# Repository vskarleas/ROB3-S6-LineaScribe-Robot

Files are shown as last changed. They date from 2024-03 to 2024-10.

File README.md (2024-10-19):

# Projet ROB3: Rami, Yannis, Vasilis

## Description

On the S6 at polytech Sorbone (Robotics Engineering major) students are required to develop a robotic system from Scratch. Below is my realisation and development of such a robot that is called LineaScribe. For more information about the project objectives for the 2023-2024 academic year, visit the following link:  
[Robot objectives](https://wiki.fablab.sorbonne-universite.fr/BookStack/books/projets-due-2023-2024/page/le-sujet-du-projet). 

You can find the Fablab Wiki link of the project [here](https://wiki.fablab.sorbonne-universite.fr/BookStack/books/projets-due-2023-2024/page/projet-rob3-rami-yannis-vasilis)

---

## **LineaScribe Robot**

### **Informations**

#### Membres

| Nom Prénom | Email |
| --- | --- |
| TOBBAL Yannis | [tobbalya@gmail.com](mailto:tobbalya@gmail.com) |
| ARIDI Rami | [rami.aridi@etu.sorbonne-universite.fr](mailto:rami.aridi@etu.sorbonne-universite.fr) |
| SKARLEAS Vasileios Filippos | [vasileios.skarleas@etu.sorbonne-universite.fr]() |

#### Cursus

Polytech 3eme année | Spécialité: Robotique

#### Délais

Début: 14/02/24 | Fin: 23/05/24

### **But, objectifs et contexte**

#### But

Le but est de créer un robot capable de dessiner différentes formes sur une feuille de papier. Il doit pouvoir réaliser des formes préprogrammée ainsi qu'être contrôlé manuellement.

Le robot est fixé sur un support carré horizontal comportant une zone de dessin de 10\*10 cm. Il y a 2 exercice qu'il doit réussir. En outre, le robot faut être capable de répondre au cahier des charges disponible `<span style="text-decoration: underline;">`[ici](https://wiki.fablab.sorbonne-universite.fr/BookStack/books/projets-due-2023-2024/page/le-sujet-du-projet).

**`<span style="text-decoration: underline;">`Exercice 1
***Dessiner des formes prédéfinies*

Le robot doit être capable de réaliser en 10 +- 0.2 secondes:

-Une ligne droite de 5cm
-Une ligne droite de 5cm en pointillés
-Un cercle de 2.5cm de rayon
-Un cercle de 2.5cm de rayon en pointillés

`<span style="text-decoration: underline;">`**Exercice 2** *Permettre à un utilisateur de dessiner*`<span style="text-decoration: underline;">`

L'utilisateur doit être capable d'utiliser le robot pour dessiner la forme qu'il veut sur la zone de dessin. Le robot est contrôlé par un joystick qui doit donc être doté des fonctions utilisés dans l'exercice 1 (Déplacement, relever le stylo etc...)

#### Besoins

Il faut donc créer un robot qui:

- Maintienne un effecteur (le stylo) afin de dessiner
- Se déplace:
  - Dans un plan horizontal: Créer les formes
  - Verticalement: Dessiner ou non, pour les pointillés
- Enregistre des formes prédéfinies
- Soit capable d'être contrôlé précisément par le joystick

#### Matériel

Les moyens qu'on a à notre disposition sont les suivantes:

- Un crayon
- Interface de commande :
  - Une carte arduino UNO avec câble USB-B;
  - Un joystick:
  - Une platine de protoypage;
  - Alimentation régulée 5V ;
  - Câbles, LEDs, boutons poussoirs, résistances.
- Motorisation :
  - Deux servomoteurs HS422 180°;
  - Un servomoteur Emax ES08A 180°.
- Mécanique :
  - Matière PLA pour impression 3D;
  - Feuilles MDF : 3mm et 6mm d'épaisseur;
  - Vis et écrous : M2, M2.5, M3, M4.
  - Roulements et axes de diamètre 4mm.
- Informatique
  - Ressources CAO.zip contient les fichiers Solidworks pour les deux modèles de servomoteurs
  - datasheets.zip contient les documentations de quelques-uns des composants fourni

#### Machines utilisées

Utilisation de l'impression 3D pour des pièces sophistiquée et éventuellement de la technologie de découpe laser pour les autres pièces.

##### Matière consommée:

MDF: 64 cm`<sup>`3 `</sup>`(Bras) + 302 cm`<sup>`3 `</sup>`(Tour): 366 cm`<sup>`3`</sup>` total
PLA: 7.3 cm`<sup>`3 `</sup>`(Effecteur) + 9 cm`<sup>`3 `</sup>`(Actionneur) : 16.3 cm`<sup>`3 `</sup>`total

### **Diagramme de GANTT**

Il y a un lien interactif qui est mis à jour à chaque modification via [https://airtable.com/appVydj1BDLSFj432/shrm5Cjk0diMBPmgL](https://airtable.com/appVydj1BDLSFj432/shrm5Cjk0diMBPmgL)

(https://wiki.fablab.sorbonne-universite.fr/BookStack/uploads/images/gallery/2024-02/project-fablab-rob3-tasks-1.png)(https://wiki.fablab.sorbonne-universite.fr/BookStack/uploads/images/gallery/2024-02/project-fablab-rob3-tasks-2.png)

<p class="callout info">**Nota bene**  
Ce diagramme de GANTT est donnée à titre indicatif</p>

[Project FabLab ROB3 Tasks (GANTT).pdf](https://wiki.fablab.sorbonne-universite.fr/BookStack/attachments/549)

### **Étape 1: Brainstorming, idées de réalisation et analyse des risques**

Durant notre brainstorming: nous eûmes 5 idées que nous avons ultimement rejetées:

[`<span style="color: rgb(35, 111, 161);">`*Figure 1: Photo de notre tableau - juste pour démonstration. Explications sont disponibles ci-dessous*](https://wiki.fablab.sorbonne-universite.fr/BookStack/uploads/images/gallery/2024-02/img-6529.png)

`<span style="color: rgb(34, 34, 34); font-family: var(--font-heading, var(--font-body)); font-size: 1.666em; font-weight: 400;">`Idée 1 - Robot de roues

`<span style="text-decoration: underline;"><span style="color: rgb(0, 0, 0);">`Principe:

Un robot sur deux roues motorisées. Il peut faire de rotations en faisant tourner ses roues dans des directions opposées

- Le stylo est attaché au centre de de la plateforme.
- Les roues seraient contrôlées grâce aux 2 servomoteurs HS422 d'une façon similaire au robot E-PUC. Les servomoteurs sont connectés à la plateforme et aux roues via des biellettes ou des engrenages.
- Un servomoteur ES08A est utilisé pour contrôler le mécanisme de levée et de descente du stylo. Ce servomoteur est plus petit que les HS422 et peut être monté sur la plateforme à proximité du stylo.

`<span style="text-decoration: underline;"><span style="color: rgb(0, 0, 0);">`Croquis:

[](https://wiki.fablab.sorbonne-universite.fr/BookStack/uploads/images/gallery/2024-03/screenshot-2024-03-02-at-2-31-25-pm.png)[`<span style="color: rgb(126, 140, 141);"><span style="color: rgb(35, 111, 161);">`*Figure 2: Croquis du robot de* roues (type voiture avec une bille pour la stabilisation)](https://wiki.fablab.sorbonne-universite.fr/BookStack/uploads/images/gallery/2024-03/screenshot-2024-03-02-at-2-31-25-pm.png)

`<span style="text-decoration: underline;"><span style="color: rgb(0, 0, 0);">`Avantages:

- `<span style="color: rgb(0, 0, 0);">`Le robot est facile à contrôler avec un joystick (important pour la réalisation de l’exercice 2)
- `<span style="color: rgb(0, 0, 0);">`Sa construction et modélisation est simple

`<span style="text-decoration: underline;"><span style="color: rgb(0, 0, 0);">`Inconvénients: 

- On ne peut pas réaliser de trajectoires complexes. Le robot ne peut pas suivre des trajectoires complexes sans l'aide de capteurs odométrique.
- L'utilisation des servomoteurs empêcherait de faire rouler le robot indéfiniment. Cela ne serait pas un problème avec l'exercice 1. L'exercice 2 pourrait se révéler impossible à faire (Prenons par exemple un cas hyperbolique et fantaisiste: La forme à dessiner au joystick est une réplique de la Joconde. Le robot ne pourrait jamais faire ceci). Pour dépasser cet obstacle, il faudrait utiliser de roues avec une diamètre assez grande entraînant des complications aux glissements sur la surface.

#### Idée 2 - Robot XY (cartésien)

`<span style="text-decoration: underline;"><span style="color: rgb(0, 0, 0);">`Principe:

Un système similaire au fonctionnement d'une imprimante 3D:

- A l'aide d'un système de bielle manivelle, les deux servomoteurs HS422 commandent des liaisons glissières sur les axes x et y.
- La bielle tenant le stylo est elle même tenue par une bielle. Cette dernière se positionne sur la coordonnée de son axe, tandis que la bielle de l'effecteur choisit alors la deuxième coordonnée du point.
- Le servomoteur ES08A commande la levée et descente du stylo

`<span style="text-decoration: underline;"><span style="color: rgb(0, 0, 0);">`Croquis:

[image (1).png*Figure 3: Le croquis d'un robot cartésien*](https://wiki.fablab.sorbonne-universite.fr/BookStack/uploads/images/gallery/2024-03/image-1.png)

`<span style="text-decoration: underline;"><span style="color: rgb(0, 0, 0);">`Avantages:

- Cette solution ne présente pas de singularités dans sa configuration. De plus, les calculs sont simplifiés par le fait qu'on ne réfléchisse que sur le plan cartésien. Ce qui signifie qu'il peut atteindre toutes les positions du plan cartésien.
- Ce système permet un mouvement fluide et précis du stylo.
- Les calculs pour contrôler le robot sont simplifiés par le fait qu'on ne réfléchit que sur le plan cartésien sans faire ce changements de `<span style="color: rgb(0, 0, 0);">`bases.

`<span style="text-decoration: underline; color: rgb(0, 0, 0);">`Inconvénients:

- Le système de bielle-manivelle peut être plus lourd qu'un système à roues motorisées, ce qui peut affecter la performance du robot.
- Le système de bielle manivelle pourrait se révéler trop massif pour le robot.
- La solution consommerait beaucoup de matière

#### Idée 3 - Scissors mecanism

`<span style="text-decoration: underline; color: rgb(0, 0, 0);">`Principe:

Inspirés du "Scissors mechanism", on voudrait attacher deux servomoteurs à la base du mécanisme et un système de commande d'actionneur au point "STYLO". Cette solution présente des avantages telles que :

`<span style="text-decoration: underline; color: rgb(0, 0, 0);">`Croquis:

[image (3).png*Figure 4: Démonstration du mécanisme de ciseaux*](https://wiki.fablab.sorbonne-universite.fr/BookStack/uploads/images/gallery/2024-03/image-3.png)

`<span style="text-decoration: underline;"><span style="color: rgb(0, 0, 0); text-decoration: underline;">`Avantages:

- Le mécanisme "Scissors" permet d'avoir un espace d'écriture plus grand que les systèmes à roues motorisées ou à bielle-manivelle. Cela est dû à la tendance du mécanisme à s'étendre.
- De plus, ce mécanisme est particulièrement adapté à la création de cercles. La rotation des bras permet de dessiner des cercles de différentes tailles avec précision.
- En outre, le mécanisme "Scissors" permet de dessiner des lignes droites très précises dans le sens du mouvement du stylo.

`<span style="text-decoration: underline; color: rgb(0, 0, 0);">`Inconvénients:

- Malheureusement, cette solution présente également un inconvénient. Les mouvements étant plutôt révolutionnaires, créer des lignes droites verticales du stylo semble limité et dans certains cas extrêmes impossible.

#### Idée 4 - Point d'intersection

`<span style="text-decoration: underline; color: rgb(0, 0, 0);">`Principe:

Le robot sera doté d'un mécanisme de ciseaux alimenté par deux servomoteurs positionnés aux coins de la base d'écriture. Chacun entraînera la rotation d'une poutre, permettant des mouvements de glissement dans les deux directions du vecteur r de rotation,. Le point d'intersection des deux poutres (créant ainsi une liaison glissière complexe) serait équipé du stylo, assurant une couverture totale de la feuille grâce à cette configuration ingénieuse.

`<span style="text-decoration: underline; color: rgb(0, 0, 0);">`Croquis:

[*Figure 5: Une conception de l'idée de point d'intersection*](https://wiki.fablab.sorbonne-universite.fr/BookStack/uploads/images/gallery/2024-02/file-000.png)

`<span style="text-decoration: underline; color: rgb(0, 0, 0);">`Inconvénients:

- L'effort tangent au mouvement du stylo généré par une poutre sur l'autre serait extrêmement important, dépassant probablement les limites de faisabilité. La nécessité d'un glissement ultra-lisse, sans aucun frottement, et d'une précision extrême dans les mouvements représente un défi technique considérable.

#### Idée 5 - Robot type SCARA

`<span style="text-decoration: underline; color: rgb(0, 0, 0);">`Principe:

On a pensé de faire un robot qui a deux axes de rotation verticales et une axe de rotation horizontale. En fait, il y aura deux rotations autour de deux axes Z (Z1 et Z2) verticales et une troisième rotation autour de Z3 qui est perpendiculaire au axe (Z2).

`<span style="text-decoration: underline;">`Croquis:

[image (2).png*Figure 6: croquis du robot avec 2 dégrées de liberté*](https://wiki.fablab.sorbonne-universite.fr/BookStack/uploads/images/gallery/2024-03/image-2.png)

`<span style="text-decoration: underline;">`Avantages:

- C'est un modèle connu du groupe, la partie mathématique est donc plus simple à réaliser
- Il y a beaucoup de manières de retirer de la matière avec une modélisation intelligente.

`<span style="text-decoration: underline;">`Inconvénients:

- Poids excessive sur l'endroit du moteur 2, quelque chose qui pourrait impacter la précision de designs. Idéalement, on voudrait trouver une solution qui permettra de déplacer ce moteur sur le corps de la base principale du robot (où se trouve le moteur 1) en utilisant les outils qu'on a à notre disposition.

#### Idée 6 - Robot parallélépipède

`<span style="text-decoration: underline;">`Principe:

Inspiré par le mécanisme du robot type SCARA, on avait une réflexion: "Pourquoi on ne déplace pas le moteur de la 2éme rotation (moteur2), sur le même axe de rotation qui celui du moteur 1. Le résultat du mouvement sera la même tout en ayant déplacé la majorité du poids sur le corps principale du robot.

`<span style="text-decoration: underline;">`Croquis:

[Figure 7: Croquis du robot parallélépipède](https://wiki.fablab.sorbonne-universite.fr/BookStack/uploads/images/gallery/2024-03/Km2image.png)

`<span style="text-decoration: underline;">`Avantages:

- Moins de poids sur les articulations mobiles du robot =&gt; meilleur précision par rapport l'idée d'avant.

`<span style="text-decoration: underline;">`Inconvénients:

- Selon la manière d'expression du modèle géométrique direct, le calcul du modèle géométrique inverse pourrait être compliqué.
- La modélisation des quelques pièces unique pour la réalisation de ce type du robot pourrait augmenter le temps de fabrication et l'utilisation de matière.

#### Solution retenue

Ayant effectué une évaluation approfondie des différentes alternatives, notre équipe a choisi de privilégier le développement d'un robot type parallélépipède pour la prochaine étape du projet. Cette décision est basée sur plusieurs points clés :

1. Robot de roues

   - Pour s'assurer de la validité de la trajectoire, il faudrait l’équiper de capteurs odométrique. Nous ne disposons pas de ce matériel
   - L'utilisation des servomoteurs empêcherait de faire rouler le robot indéfiniment. Cela ne serait pas un problème avec l'exercice 1. L'exercice 2 pourrait se révéler impossible à faire (Prenons par exemple un cas hyperbolique et fantaisiste: La forme à dessiner au joystick est une réplique de la Joconde. Le robot ne pourrait jamais faire ceci)
2. Robot XY

   - Le système de bielle manivelle pourrait se révéler trop massif pour le robot.
   - La solution consommerait beaucoup de matière
3. Robot "scissors"

   - Selon la mécanique de la pièce, la création des lignes droites perpendiculaires du stylo n'est pas toujours possible à cause des mouvements révolutionnaires du mécanisme
   - Les déplacement sont limités à des trajectoires bien précises, ce qui rend le contrôle au joystick frustrant.
4. Robot intersection

   - Il s'agit d'une idée très complète. Cependant, lorsque l'effecteur se trouve à l'extrémité des deux axes de guidage, il faut exercer une force massive pour l'en sortir et le faire revenir près des moteurs.Nous pourrions contourner ce problème en faisant en sorte que les axes soient bien plus grand que la zone de travail. Mais:
     - Cela impliquerait un ajout de matière, et donc de masse
     - Cela n'empêcherait pas un utilisateur au joystick de bloquer le robot
5. Robot type SCARA

   - Il s'agit de notre idée de départ de base, mais à la découverte de l'idée numéro 6 qui nous permettra de déplacer les deux moteur sur le corps de la base du robot, on a décidé de développer le robot type parallélépipède.

### **Étape 2: Conception détaillée**

#### Modèle géométrique

<p class="callout info">**Nota bene** On avait déjà commencé l'analyse du modèle cinématique du robot de l'idée numéro 5 (type SCARA). Ci-dessous vous allez trouver l'option également de visualiser et voir le calcul qui était effectué pour ce robot, ainsi que pour le robot type parallélépipède (idée numéro 6).  
Les équations trouvées dans le modèle parallélépipède étant impossible à résoudre, on se base d'abord sur celles du SCARA tout en adaptant ces-dernières aux spécificités de notre modèle  
</p>

<details id="bkmrk-robot-type-scara-cin"><summary>Robot type SCARA</summary>

### Cinématique

#### Schéma Cinématique + Tableau DH

<table border="1" id="bkmrk-solid-%CE%B8i%2B1-di%2B1-ai-%CE%B1" style="border-collapse: collapse; width: 100%;"><colgroup><col style="width: 20.0247%;"></col><col style="width: 20.0247%;"></col><col style="width: 20.0247%;"></col><col style="width: 20.0247%;"></col><col style="width: 20.0247%;"></col></colgroup><tbody><tr><td data-sheets-value="{"1":2,"2":"Solid"}" style="overflow: hidden; padding: 2px 3px 2px 3px; vertical-align: bottom;">**Solid**</td><td data-sheets-value="{"1":2,"2":"θi+1"}" style="overflow: hidden; padding: 2px 3px 2px 3px; vertical-align: bottom;">**ai**</td><td data-sheets-value="{"1":2,"2":"di+1"}" style="overflow: hidden; padding: 2px 3px 2px 3px; vertical-align: bottom;">**αi**</td><td data-sheets-value="{"1":2,"2":"ai"}" style="overflow: hidden; padding: 2px 3px 2px 3px; vertical-align: bottom;">**di+1**</td><td data-sheets-value="{"1":2,"2":"αi"}" style="overflow: hidden; padding: 2px 3px 2px 3px; vertical-align: bottom;">**θi+1**</td></tr><tr><td class="align-right" data-sheets-value="{"1":3,"3":0}" style="overflow: hidden; padding: 2px 3px 2px 3px; vertical-align: bottom; text-align: right;">0</td><td class="align-right" data-sheets-value="{"1":2,"2":"θ1"}" style="overflow: hidden; padding: 2px 3px 2px 3px; vertical-align: bottom;">0</td><td class="align-right" data-sheets-value="{"1":2,"2":"h1"}" style="overflow: hidden; padding: 2px 3px 2px 3px; vertical-align: bottom;">0</td><td class="align-right" data-sheets-value="{"1":3,"3":0}" style="overflow: hidden; padding: 2px 3px 2px 3px; vertical-align: bottom; text-align: right;">h1</td><td class="align-right" data-sheets-value="{"1":3,"3":0}" style="overflow: hidden; padding: 2px 3px 2px 3px; vertical-align: bottom; text-align: right;">θ1</td></tr><tr><td class="align-right" data-sheets-value="{"1":3,"3":1}" style="overflow: hidden; padding: 2px 3px 2px 3px; vertical-align: bottom; text-align: right;">1</td><td class="align-right" data-sheets-value="{"1":2,"2":"θ2"}" style="overflow: hidden; padding: 2px 3px 2px 3px; vertical-align: bottom;">L1</td><td class="align-right" data-sheets-value="{"1":2,"2":"h2"}" style="overflow: hidden; padding: 2px 3px 2px 3px; vertical-align: bottom;">-π/2</td><td class="align-right" data-sheets-value="{"1":2,"2":"L1"}" style="overflow: hidden; padding: 2px 3px 2px 3px; vertical-align: bottom;">h2</td><td class="align-right" data-sheets-value="{"1":3,"3":0}" style="overflow: hidden; padding: 2px 3px 2px 3px; vertical-align: bottom; text-align: right;">θ2-π/2</td></tr><tr><td class="align-right" data-sheets-value="{"1":3,"3":2}" style="overflow: hidden; padding: 2px 3px 2px 3px; vertical-align: bottom; text-align: right;">2</td><td class="align-right" data-sheets-value="{"1":2,"2":"-π/2"}" style="overflow: hidden; padding: 2px 3px 2px 3px; vertical-align: bottom;">0</td><td class="align-right" data-sheets-value="{"1":3,"3":0}" style="overflow: hidden; padding: 2px 3px 2px 3px; vertical-align: bottom; text-align: right;">0</td><td class="align-right" data-sheets-value="{"1":2,"2":"L2"}" style="overflow: hidden; padding: 2px 3px 2px 3px; vertical-align: bottom;">L2</td><td class="align-right" data-sheets-value="{"1":2,"2":"-π/2"}" style="overflow: hidden; padding: 2px 3px 2px 3px; vertical-align: bottom;">θ3</td></tr></tbody></table>

Schema cinématique du robot type SCARA (https://wiki.fablab.sorbonne-universite.fr/BookStack/uploads/images/gallery/2024-02/img-0149.jpeg)Les deux premières liaisons, pour 𝑖∈{1,..,2}, sont des liaisons pivot d’axe (𝑂𝑖,𝑧𝑖). La troisième liaison est une liaison pivot d'axe aussi selon z3.

#### Modèle géométrique directe (complet)

Calculant T`<sub>`0-&gt;1`</sub>`, T`<sub>`1-&gt;2`</sub>`, T`<sub>`2-&gt;effector`</sub>`, ainsi que T`<sub>`0-&gt;effector`</sub>`.

(https://wiki.fablab.sorbonne-universite.fr/BookStack/uploads/images/gallery/2024-03/equations-scara-1.png)

Equations scara-2.jpg (https://wiki.fablab.sorbonne-universite.fr/BookStack/uploads/images/gallery/2024-03/equations-scara-2.png)

Les résultas sont disponibles en PDF sur: [Matrices de transformation homogene.pdf](https://wiki.fablab.sorbonne-universite.fr/BookStack/attachments/571)

#### Modèle géométrique directe (simplifié)

On peut aussi se concentrer uniquement sur les deux premières rotations car ce sont elles qui donneront la position finale du stylo. Après un moment donné pour écrire ou non, on peut configurer cela en programmation. De cette façon, nous pouvons simplifier le calcul comme ci-dessous :

SCARA Simplified Robot-1.png (https://wiki.fablab.sorbonne-universite.fr/BookStack/uploads/images/gallery/2024-03/scara-simplified-robot-1.png)

SCARA Simplified Robot-2.jpg (https://wiki.fablab.sorbonne-universite.fr/BookStack/uploads/images/gallery/2024-03/scara-simplified-robot-2.jpg)

Les résultats sont disponibles en PDF sur: [SCARA Simplified Robot.pdf](https://wiki.fablab.sorbonne-universite.fr/BookStack/attachments/578)

#### Modèle géométrique inverse

Ainsi selon le modèle géométrique directe et le la trigonométrie du systéme:

Screenshot 2024-03-02 at 9.47.31 PM.png (https://wiki.fablab.sorbonne-universite.fr/BookStack/uploads/images/gallery/2024-03/screenshot-2024-03-02-at-9-47-31-pm.png)

Screenshot 2024-03-02 at 9.47.18 PM.png (https://wiki.fablab.sorbonne-universite.fr/BookStack/uploads/images/gallery/2024-03/screenshot-2024-03-02-at-9-47-18-pm.png)

</details><details id="bkmrk-robot-type-parall%C3%A9l%C3%A9"><summary>Robot type parallélépipède</summary>

#### Modèle géométrique directe

Ci-dessous, vous trouverez l'approche mathématique du robot type parallélépipède pour sa modèle géométrique directe.

(https://wiki.fablab.sorbonne-universite.fr/BookStack/uploads/images/gallery/2024-03/parallelipede-1.png)

(https://wiki.fablab.sorbonne-universite.fr/BookStack/uploads/images/gallery/2024-03/parallelipede-2.png)

Les résultats sont disponibles en PDF sur: [Parallélépipède Robot.pdf](https://wiki.fablab.sorbonne-universite.fr/BookStack/attachments/572)

</details><details id="bkmrk-sp%C3%A9cifications-de-no"><summary>Spécifications de notre modéle</summary>

Avant trouver l'angle θ2 final, il faut procéder au choix de notre sens du plan, qui dépend de la configuration du robot et de l'angle θ1. Le calcul suivant nous permet d'obtenir la formule final de l'angle θ2:

(https://wiki.fablab.sorbonne-universite.fr/BookStack/uploads/images/gallery/2024-04/image-1.png)

</details>
#### Schéma électronique

Sur notre schéma électronique il y a un bouton qui permet de changer entre mode manuelle et mode automatique. De plus, il y a deux LED qui indiquent sur quel mode on est un moment donné. Par exemple si on est en mode manuelle, la LED bleue est allumée, sinon la LED verte est allumée. En outre, vous pouvez aussi trouver la connexion du joystick analogique dont on a besoin pour la réalisation de l'exercice 2. Il faut noter que le joystick à un fonctionnement de bouton intégré. On peut utiliser cette fonctionnalité pour contrôler plein de différentes choses, par exemple:

- Le stylo écrit ou pas.
- On fait un dessin avec le joystick qu'on visualise sur l'écran de l'ordinateur et on tape le bouton pour confirmer le dessin afin qu'il est créé par le robot.

(https://wiki.fablab.sorbonne-universite.fr/BookStack/uploads/images/gallery/2024-05/CFNlineascript.png)

[Figure 8: Schéma électronique V1.5.0](https://wiki.fablab.sorbonne-universite.fr/BookStack/uploads/images/gallery/2024-05/CFNlineascript.png)

Une version optimisée pour plus de clarté et incluant les fonctions carré et joystick processing sera publiée prochainement

#### Modélisation

Notre objectif principal était de modéliser le robot selon un design à la fois compact et rigide. Un autre aspect important était de minimiser la quantité de matière utilisée et de réduire au maximum le temps de fabrication. Un modèle assemblé sur SolidWorks est disponible ci-dessous.

[Figure 9: Démonstration du mécanisme du robot LineaScribe](https://wiki.fablab.sorbonne-universite.fr/BookStack/uploads/images/gallery/2024-03/displayrobot.gif)

##### Sous-assemblages

1. Bâti support
2. Articulations parallèles
3. Pivot joint
4. Pivot motor
5. Axe d'effecteur
6. Effecteur

##### Bâti support

C'est le corps principal du robot. Son objectif principal est de maintenir les deux moteurs sur le même axe de rotation. Il doit être capable de supporter les forces exercées par les moteurs vers les articulations parallèles ainsi que le retour des forces de frottement.

[Screenshot 2024-03-09 at 8.15.57 PM.pngFigure 10: Bâti support du robot avec les moteur assemblés](https://wiki.fablab.sorbonne-universite.fr/BookStack/uploads/images/gallery/2024-03/screenshot-2024-03-09-at-8-15-57-pm.png)

Le bâti est entièrement créé en utilisant la découpe laser. Concernant la conception de la pièce, il faut noter que le plan du moteur du haut (moteur 1) est conceptualisé de manière à ne pas permettre le détachement des pièces tout en acceptant un stress excessif par les articulations principales du robot.

##### Articulations parallèles (billettes)

Elles sont également entièrement conceptualisées pour la découpe laser (3 couches différentes de 3 mm). Elles sont montées sur les pièces "pivot joint" et "pivot motor" en utilisant des roulements 7201 BEGAP. Elles sont:

<table border="1" id="bkmrk-billette-principale-" style="border-collapse: collapse; width: 100%; height: 59.5938px;"><colgroup><col style="width: 50%;"></col><col style="width: 50%;"></col></colgroup><tbody><tr style="height: 29.7969px;"><td style="height: 29.7969px;">**Billette Principale**</td><td style="height: 29.7969px;">**Billette Secondaire**</td></tr><tr style="height: 29.7969px;"><td style="height: 29.7969px;">Screenshot 2024-03-10 at 7.41.27 PM.png (https://wiki.fablab.sorbonne-universite.fr/BookStack/uploads/images/gallery/2024-03/screenshot-2024-03-10-at-7-41-27-pm.png)</td><td style="height: 29.7969px;">Screenshot 2024-03-10 at 7.42.18 PM.png (https://wiki.fablab.sorbonne-universite.fr/BookStack/uploads/images/gallery/2024-03/screenshot-2024-03-10-at-7-42-18-pm.png)</td></tr></tbody></table>

##### Pivot joint

Son rôle et la précision d'application sont essentiels pour le bon fonctionnement du robot. Il nous permet d'obtenir la distance correcte en parallélisme, comme indiqué dans le design ci-dessous. Il est entièrement créé en utilisant la découpe laser (2 couches de 3 mm).

[Screenshot 2024-03-09 at 8.06.04 PM.pngFigure 11: Focalisation sur la pièce &#34;pivot joint&#34;](https://wiki.fablab.sorbonne-universite.fr/BookStack/uploads/images/gallery/2024-03/8vMscreenshot-2024-03-09-at-8-06-04-pm.png)

##### Pivot motor

C'est la seule pièce qui est modélisée pour l'impression 3D. Son rôle est le même que celui de la pièce "pivot joint". Elle est directement montée sur le moteur du bas (moteur 2). Pour renforcer la partie de la pièce qui recevra les forces de frottement du stylo, un triangle de renfort a été ajouté, comme vous pouvez le voir ci-dessous.

[Screenshot 2024-03-09 at 8.12.07 PM.pngFigure 12: Triangle de renfort de &#34;pivot motor&#34;](https://wiki.fablab.sorbonne-universite.fr/BookStack/uploads/images/gallery/2024-03/screenshot-2024-03-09-at-8-12-07-pm.png)

<p class="callout info">L'axe centrique est un détail et il n'est pas requis pour le fonctionnement correct du mécanisme.</p>

<table border="1" id="bkmrk--13" style="border-collapse: collapse; width: 100%; height: 191.422px;"><colgroup><col style="width: 33.3539%;"></col><col style="width: 33.3539%;"></col><col style="width: 33.3539%;"></col></colgroup><tbody><tr style="height: 191.422px;"><td style="border-style: none; height: 191.422px;">Screenshot 2024-03-09 at 8.11.43 PM.png (https://wiki.fablab.sorbonne-universite.fr/BookStack/uploads/images/gallery/2024-03/screenshot-2024-03-09-at-8-11-43-pm.png)</td><td style="height: 191.422px; border-style: none;">Screenshot 2024-03-09 at 8.12.13 PM.png (https://wiki.fablab.sorbonne-universite.fr/BookStack/uploads/images/gallery/2024-03/screenshot-2024-03-09-at-8-12-13-pm.png)</td><td style="height: 191.422px; border-style: none;">Screenshot 2024-03-09 at 8.12.22 PM.png (https://wiki.fablab.sorbonne-universite.fr/BookStack/uploads/images/gallery/2024-03/screenshot-2024-03-09-at-8-12-22-pm.png)</td></tr></tbody></table>

##### Axe d'effecteur (billette Emax)

Il s'agit de l'axe qui supporte l'outil de l'effecteur. Il est guidé par les axes parallèles et mis en position (MIP) par la pièce "pivot joint". Le moteur est mis en position grâce à "Pignon Servo Emax". C'est la plateforme sur laquelle on fixe le moteur Emax comme on peut observer ci-dessous :

[Screenshot 2024-03-10 at 7.50.44 PM.pngFigure 13: Billette Emax en assemblage avec le moteur 3 (Emax)](https://wiki.fablab.sorbonne-universite.fr/BookStack/uploads/images/gallery/2024-03/screenshot-2024-03-10-at-7-50-44-pm.png)

[Screenshot 2024-03-10 at 8.59.03 PM.pngFigure 14: Modèle d&#39;un pignon servo Emax](https://wiki.fablab.sorbonne-universite.fr/BookStack/uploads/images/gallery/2024-03/screenshot-2024-03-10-at-8-59-03-pm.png)

##### Effecteur

L'outil de l'effecteur est l'élément terminal du robot qui entre en contact direct avec la surface d'écriture. Son rôle principal est de tracer des lignes en utilisant un stylo. Voici la deuxième pièce en impression 3D :

[Screenshot 2024-03-10 at 9.00.51 PM.pngFigure 15: La pièce qui va soutenir l&#39;outil (le stylo dans notre cas)](https://wiki.fablab.sorbonne-universite.fr/BookStack/uploads/images/gallery/2024-03/screenshot-2024-03-10-at-9-00-51-pm.png)

##### Solidworks

Tous les fichiers et les fichiers d'assemblage sont disponibles sur: [LineaScribe Robot.zip](https://wiki.fablab.sorbonne-universite.fr/BookStack/attachments/620). Voici l'organisation des fichiers :

- **Architecture :** il s'agit d'un fichier squelette des différentes configurations. Si vous changez les dimensions des pièces présentes dans ce squelette, elles sont mises à jour dans tous les assemblages.
- **Assemblage bras &gt; Pièce Liaison Billette Principale - Billette Emax :** C'est notre "pivot joint"
- **Assemblage bras &gt; ActionneurServo :** C'est notre "motor joint"
- **Assemblage bras &gt; Billette \* :** ils sont les différents billettes du robot
- **Assemblage bras &gt; Pignon servo max :** c'est pour la mise en position du moteur Emax commet on peut voir à la figure
- **Assemblage bras &gt; Liaison axe :** il s'agit de l'assemblage complet du mécanisme qui va se visser sur les actionneurs.
- **Assemblage &gt; Assemblage1 :** il s'agit de l'assemblage total du robot.
- **Assemblage bras &gt;** **Effecteur :** C'est notre "effecteur"

##### Fichiers SVG &amp; STL

1. [batis.svg](https://wiki.fablab.sorbonne-universite.fr/BookStack/attachments/609) (MDF 6mm)
2. [pivot joint.svg](https://wiki.fablab.sorbonne-universite.fr/BookStack/attachments/610) (MDF 3mm)
3. [bilette1.svg](https://wiki.fablab.sorbonne-universite.fr/BookStack/attachments/611) - articulation parallèle 1 - billette principale (MDF 3mm)
4. [bilette2.svg](https://wiki.fablab.sorbonne-universite.fr/BookStack/attachments/612) - articulation parallèle 2 - billette secondaire (MDF 3mm)
5. [pivot motor.STL](https://wiki.fablab.sorbonne-universite.fr/BookStack/attachments/613) (3D Maker PLA 30% infill - no support)
6. [bilette3 et pignon EMAX.svg](https://wiki.fablab.sorbonne-universite.fr/BookStack/attachments/638) (MDF 3mm)
7. [Effecteur.STL](https://wiki.fablab.sorbonne-universite.fr/BookStack/attachments/662) (PLA 1.75mm)

#### Modèle géométrique inverse: vérification

D'après le calcul des robots de type parallélépipède et SCARA, nous avons développé un script sur MATLAB permettant de vérifier le calcul des coordonnées du plan cartésien x, y en fonction des angles θ1 et θ2.

Notre analyse a permis de conclure que :

- Dans le cadre de la limitation de l'espace d'écriture de la plateforme, il existe parfois plusieurs solutions possibles pour atteindre une position spécifique. Il ne s'agit pas de singularités, mais plutôt de libertés de rotation autour des axes des moteurs. Cependant, le robot ne peut pas se placer à certains endroits en raison de la modélisation (support du moteur 1).
- Il est donc nécessaire de trouver une procédure permettant de choisir la solution du système qui est acceptable.

Voici le fichier MATLAB: [MGI\_matlab.m](https://wiki.fablab.sorbonne-universite.fr/BookStack/attachments/615)

Pour utiliser le fichier il suffit d'appeler la fonction MGI\_matlab, et passer comme arguments les coordonnées x, y et L1 et L2 les longueurs des articulations du robot. On a ci-dessous le résultat lorsqu'on exécute la fonction pour obtenir les 4 sommets d'un carré (5cm) et qu'on entre les angles renvoyés dans notre esquisse du bras.

(https://wiki.fablab.sorbonne-universite.fr/BookStack/uploads/images/gallery/2024-05/demo.png)

#### Pre-requis

Lors du montage du robot, les moteurs doivent être calibrés. Nous vous conseillons de mettre les moteurs en position 0 degré (servo 1) et 90 degrés (servo 2). Ensuite, levez le bras à une position de 90 degrés. Attention, servo1 et servo2 sont les références dans le code disponible ci-dessous.

```c++
void setup()
{
  ...
servo1.write(0);
servo2.write(90);
  ...
}
```

#### Pistes de programmation

##### Organigramme:

`<span style="text-decoration: underline;">`Programme principal (Setup+Loop)



`<span style="text-decoration: underline;">`Ligne Droite

Straight Line.png (https://wiki.fablab.sorbonne-universite.fr/BookStack/uploads/images/gallery/2024-05/straight-line.png)

`<span style="text-decoration: underline;">`Ligne Pointillées

`<span style="text-decoration: underline;">`Dotted Line.png (https://wiki.fablab.sorbonne-universite.fr/BookStack/uploads/images/gallery/2024-05/dotted-line.png)

`<span style="text-decoration: underline;">`Cercle

`<span style="text-decoration: underline;">`(https://wiki.fablab.sorbonne-universite.fr/BookStack/uploads/images/gallery/2024-05/cercle.png)

`<span style="text-decoration: underline;">`Cercle Pointillés

`<span style="text-decoration: underline;">`Dot Circle.png (https://wiki.fablab.sorbonne-universite.fr/BookStack/uploads/images/gallery/2024-05/dot-circle.png)

L'organigramme des fonctions carré et joystick a changé récemment et sera posté plus tard

#### Programmation

##### Application du modèle géométrique inverse pour calculer les angles de contrôle de moteurs

```c++
/* Takes a cartesien position (x,y) and updates the angles teta1 and teta2 that control the two motors (located on the same r) */
void get_angles(double x, double y, float L1, float L2, double* teta1, double* teta2){

  //Distance between the center of the robot and the starting point of the writing area
  x+=dx;
  y+=dy;

  //Geometric inveresed model available under teh section "Robot type SCARA"
  co2 = (x*x+y*y-L1*L1-L2*L2)/(2*L1*L2);
  teta2prec = atan2((-sqrt(1-co2*co2)),co2); //The root decides the orientation according to the configuration

  //Calculating the angle 1
  *teta1 = atan2(y,x) - atan2((L2*sin(teta2prec)),(L1+L2*cos(teta2prec)));

  teta2prec = teta2prec*180/pi; //rad to degrees 
  *teta1 = *teta1*180/pi;
  *teta2 = *teta2*180/pi;

  //teta2 is the final corrected angle according to "Specifications de notre modele" available on the Robot's documentation -> voir wiki 
  *teta2=-abs(teta2prec)+*teta1+180;

  *teta2 = 180-*teta2;
}
```

##### Control du stylo

```c++
/* Controls the tool's position [choose between UP and DOWN] */
void pen_control(int control, int *penstate) //Down, up, swithc state
{
  if (control == DOWN) //write with pen [pen is down]
  {
    servo3.writeMicroseconds(pen_down); 
    *penstate=0;
  }
  if (control == DOWN_) //write with pen [pen is down]
  {
    servo3.writeMicroseconds(pen_down_); 
    *penstate=0;
  }
  else if (control == UP) //disable writing [pen is up]
  {
    *penstate=1;
    servo3.writeMicroseconds(pen_up);
  }
  else if (control == UP_) //disable writing [pen is up]
  {
    *penstate=1;
    servo3.writeMicroseconds(pen_up_);
  }
  else if (control == SWITCH) //disable writing [pen is up]
  {
    switch(*penstate){
      case 0:
        servo3.writeMicroseconds(pen_up);
        *penstate=1;
        break;
      case 1:
        servo3.writeMicroseconds(pen_down);
        *penstate=0;
        break;
    }
  }
  else
  {
    printf("An error occured on controling the pen\n");
  }
}
```

##### Designer une ligne

```c++
/* Draws a straight line in a specific length and to a given angle */
void straight_line(double *x_start, double *y_start, float length, double angle)
{  

  //Note: We divide the distance in multiple subpoints to be acquired. The greater the number, the most precision we can achieve of course with some limitations
  for (double i = 0; i < length*900; i++)
  {
    *x_start = *x_start + cos(angle)/900; //Current position + shift  
    *y_start = *y_start + sin(angle)/900;
    get_angles(*x_start,*y_start,L1,L2,&teta1, &teta2); //calculation of motors' angles
    servo1.write(teta1); //Sending data to the motors
    servo2.write(teta2);  
    delay(1);
  }
}
```

##### Designer une ligne en pointilles

```c++
/* Designs a dotted line in a specific length */
void dotted_line(double *x_start, double *y_start, int length, double angle, float dot_length, float space_length) {
  float i=0;

  //control for the desired length
  while(i < length) {
  
    //get into writing position
    pen_control(DOWN_, &penstate);
    delay(100);
    straight_line(x_start,y_start,dot_length, angle);

    i=i+dot_length; //The length that should write a line
    if(i>=length) break;

    //Pen is on UP_ state
    pen_control(UP_, &penstate);
    delay(100);
    straight_line(x_start,y_start,space_length, angle);
    i = i + space_length; //adding the space that shouldn't write anything on the paper

  }
}
```

##### Designer un cercle

```c++
/* Designing a circle in a specific radius and a specific starting point */
void circle(double x_center, double y_center, double angle_start, double angle, double radius, double *x, double *y, int init, int res)
{

  //Placement in a specific starting point
  if(init==0){
    *x = x_center + (radius * cos(radians(angle_start)));
    *y = y_center + (radius * sin(radians(angle_start)));
    get_angles(*x,*y,L1,L2,&teta1, &teta2);
    servo1.write(teta1); 
    servo2.write(teta2); 
    delay(1000);

    //Get into writing position
    pen_control(DOWN,&penstate);
    delay(500);
  }
  
  //Repetead calculation different points between a starting angle and a final angle
  for (double i = (angle_start*res); i < (angle*res); i++)
  {
    *x = x_center + (radius * cos(radians(i/res))); //Formula of finding the position of a point is based on the tan function decomposed in x and y axis
    *y = y_center + (radius * sin(radians(i/res)));
    get_angles(*x,*y,L1,L2,&teta1, &teta2); //Calculation of angles for the motors
    servo1.write(teta1); //Sending data to the motors
    servo2.write(teta2);
    delay(1);  
  }
}
```

##### Designer un cercle en pointilles

```c++
/* Designs a dotted circle in a specific radius and a specific starting point */
void dotted_circle(double x_center, double y_center, double angle_space, double angle_dot, double radius, double *x, double *y)
{
  
  *x = x_center + (radius * cos(radians(0)));
  *y = y_center + (radius * sin(radians(0)));
  get_angles(*x,*y,L1,L2,&teta1, &teta2);
  servo1.write(teta1); 
  servo2.write(teta2); 
  delay(1000);

  //It's a recursive loop leading to a 360 degrees circle that calls circle function with a starting and final point
  double i=0.0;
  while(i < 360) {
  
    pen_control(DOWN_, &penstate);
    delay(200);
    circle(x_center, y_center,i, angle_dot+i, radius, x, y, 1, 10);
    delay(200);

    i = i + angle_dot; //update of the current position - required to verify of a circle of 360 degress has been designed

    if(i>=360) break;

    //Between delays we chage writing mode in order to create a dotted effect
    pen_control(UP, &penstate);
    delay(200);
    circle(x_center, y_center,i, (angle_space+i), radius, x, y, 1, 10);
    i = i + angle_space;
    delay(200);

  }
}
```

##### Designer un carre

```c++
/* Designs a square of a given length and in a given angle */
void square(double *x, double *y, int length, int angle)
{

  //Square is composed of four straight lines of a given length and they are vertical between them
 straight_line(x,y,length, radians(angle));
 delay(1000);
 straight_line(x,y,length, radians(angle+90));
 delay(1000);
 straight_line(x,y,length, radians(angle+180));
 delay(1000);
 straight_line(x,y,length, radians(angle+270));
 delay(1000);
}
```

##### Logique du Joystick en mode manuelle

Mode manuelle permet à l'utiliser de contrôler le robot via le Joystick tout en appuyant sur un bouton qui permet de contrôler si le stylo est en mode d'écriture ou non. Cette fonctionnalité existe sur la boucle principale comme un mode de fonctionnement. Pour rentrer dans ce mode, il suffit de presser une seule fois sur le Joystick, de même pour en sortir.

```c++
//Manual control of the robot using joystic
  if (buttonState5 == 0) {
    //Allows a smooth operation when a button is pushed (detect one time the tap)
    while (digitalRead(pinbutton1)==0){}

    digitalWrite(ledPin, HIGH);
    pen_control(UP,&penstate);
    x=0.0;
    y=0.0;
    delay(500);
    get_angles(x,y,L1,L2,&teta1, &teta2);
    servo1.write(teta1); 
    servo2.write(teta2);  
    delay(1000);

    pen_control(DOWN,&penstate);
    delay(500);

    double coef= 0.0003;
  
    while(digitalRead(pinbutton1)==1){
      //If the button is pressed then the effector is swithcing mode. For instance, if it was in writing position it goes UP and if it was UP then it gets into writing position.
      if (digitalRead(pinbutton5) == 1) {
        while (digitalRead(pinbutton5)==1){}
        pen_control(SWITCH,&penstate);
      }

      // Read analog values
      xtemp = int(512.0 - analogRead(pinx));
      ytemp = int(512.0 - analogRead(piny));

      // Apply dead zone for small movements
      if (abs(xtemp) <= 100) xtemp = 0;
      if (abs(ytemp) <= 100) ytemp = 0;

      // Update x and y coordinates
      x += xtemp * coef;
      y += ytemp * coef;

      Serial.print(x);
      Serial.print("\t");
      Serial.println(y);

      get_angles(x,y,L1,L2,&teta1, &teta2); //calculate motors' angles
      servo1.write(teta1);  //send data to the motors
      servo2.write(teta2);
      delay(10);

    }
    while (digitalRead(pinbutton1)==0){}
    digitalWrite(ledPin, LOW);
    pen_control(UP,&penstate);
    delay(500);
  }
```

##### Logique du Joystick en Processing

Les données sont traitées à l'aide d'un programme de traitement qui permet de pré-visualiser ce que vous souhaitez concevoir puis les données sont envoyées via le port série à la carte afin de contrôler les moteurs.

```c++
/* Logig for joystick manipulation */
void Joystick(double *x, double *y)
{
  int dimx=0;
  int t=0;

  //Sending mode on, sending joystick data to processing
  int out=0;
  int out1=0;
  while(out==0){

    //We check if we read the values of the Joystick where the user decided to stop (On verifie si on Lit les valeurs du Joystick ou l'utilisateur a decide d'arrete)
    if (Serial.available() > 0) {
      String response = Serial.readStringUntil('\n'); 
      response.trim();  // Remove any leading or trailing whitespace
    
      if (response.equals("Done")) {
        //digitalWrite(13,LOW);
        break;  // Stop sending data to processing
      }
    }
    //Reading Joysticks values
    xtemp = analogRead(pinx);
    ytemp = analogRead(piny);

    buttonval1 = 1-digitalRead(pinbutton1);
    buttonval2 = digitalRead(pinbutton2);

    //Sending Joysticks values to processing
    Serial.print(xtemp);
    Serial.print("\t");
    Serial.print(ytemp);
    Serial.print("\t");
    Serial.print(buttonval1); 
    Serial.print("\t");
    Serial.println(buttonval2);
  
    //This loop prevents the overlap of several values given that the frequency of sending data from the Arduino is higher than the frequency of receiving processing (Cette boucle empeche le chevauchement de plusieur valeur etant donne que la frequence d';envoi de donne de l'arduino est plus eleve que la frequence de recoit de processing)
    //We therefore wait until the data is read by processing before sending another data (On attend donc jusqu'a ce que la donnee est bien lu par processing avant d'envoyer une autre donne)
    out1=0;
    while (out1 == 0) {
      //digitalWrite(13,LOW);
      if (Serial.available() > 0) {
        String response = Serial.readStringUntil('\n'); 
        response.trim();  // Remove any leading or trailing whitespace
      
        if (response.equals("Done")) {
          out=1; //get out of the loop  //checck  andif we really get out of the loop check if it doesnt give another line of data after i wanted to start
          out1=1;
        }
        else if (response.equals("Received")) out1=1;  // Exit while loop
      }
    }
  }
  
  //tab data
  double*** tab;

  //Receive tab dimensions
  while (true) {
    if (Serial.available() > 0) {
      String receivedString = Serial.readStringUntil('\n'); // Read until newline character
      //decode data
      int rowIndex = 0;
      int colIndex = 0;
      int depthIndex = 0;

      String buffer = ""; // Buffer to hold the float string
    
      //premier element
      int i = 0;
      while(1){
        char c = receivedString.charAt(i);
        if (c == ',') {
          dimx = buffer.toInt();
          buffer = ""; // Reset buffer
        }
        else if (c == ';') {
          t = buffer.toInt();
          buffer = ""; // Reset buffer
          i++;
          break;
        }
        else {
          buffer += c; // Add character to buffer
        }
        i++;
      }

      if(t==1) digitalWrite(ledPin, LOW);

      tab = (double ***)malloc(t * sizeof(double **));
      for (int l = 0; l < t; l++) {
        tab[l] = malloc(2 * sizeof(double*)); //tableau de donne
        for (int j = 0; j < 2; j++) {
          tab[l][j] = malloc(dimx * sizeof(double));
        }
      }

      for (i; i < receivedString.length(); i++) {
        char c = receivedString.charAt(i);
        if (c == ',') {
          tab[depthIndex][rowIndex][colIndex] = buffer.toDouble();
          colIndex++;
          buffer = ""; // Reset buffer
        } else if (c == ';') {
          tab[depthIndex][rowIndex][colIndex] = buffer.toDouble();
          rowIndex++;
          colIndex = 0;
          buffer = ""; // Reset buffer
        } else if (c == '|') {
        tab[depthIndex][rowIndex][colIndex] = buffer.toDouble();
        depthIndex++;
        rowIndex = 0;
        colIndex = 0;
        buffer = ""; // Reset buffer
        } else {
          buffer += c; // Add character to buffer
        }
      }
      // Capture the last float value
      tab[depthIndex][rowIndex][colIndex] = buffer.toDouble();

      break;
    }

  }

  for (int j = 0; j < t; j++) {

      get_angles(tab[j][0][0],tab[j][1][0],L1,L2,&teta1, &teta2); //Position initiale
      servo1.write(teta1); 
      servo2.write(teta2);
      delay(1000);

      pen_control(DOWN,&penstate);
      delay(500);

    for (int i = 0; i < dimx; i++) {

      double xt = tab[j][0][i];
      double yt = tab[j][1][i];

      if(xt!=-1 && yt!=-1){
        get_angles(xt,yt,L1,L2,&teta1, &teta2);
        servo1.write(teta1); 
        servo2.write(teta2);
        delay(100);
      }
    }
    pen_control(UP,&penstate);
    delay(500);
  }

}
```

##### Initialisation

```c++
void setup() {
  servo1.attach(9);  // attaches the servo on pin 9 to the servo object
  servo2.attach(10); 
  servo3.attach(11);
  
  //declarations of different button as input ports to detect actions
  pinMode(pinx,INPUT);
  pinMode(piny,INPUT);
  pinMode(pinbutton1,INPUT_PULLUP);
  pinMode(pinbutton2,INPUT);
  pinMode(pinbutton3,INPUT);
  pinMode(pinbutton4,INPUT);
  pinMode(pinbutton5,INPUT);

  //declaration of LED pin as an output port to send commands (control if it's switched on or off)
  pinMode(ledPin,OUTPUT);

  //Get into a default starting point
  get_angles(0.0,0.0,L1,L2,&teta1, &teta2);
  servo1.write(teta1); 
  servo2.write(teta2);  

  delay(1000);
  //straight_line(&x,&y,15, radians(45));

  //Put the effector in UP position and stand by
  pen_control(UP,&penstate);

  //Start serial communication
  Serial.begin(9600);
}
```

##### Boucle principale

```c++
void loop() {  
  /* Simple implementations of existing functions for testing purposes.
  We have only one active every time. All the others has to be commented in order to observe the robot's mouvements */
  int buttonState1 = digitalRead(pinbutton5); // Read button 1 state
  int buttonState2 = digitalRead(pinbutton2); // Read button 2 state
  int buttonState3 = digitalRead(pinbutton3); // Read button 3 state
  int buttonState4 = digitalRead(pinbutton4); // Read button 4 state
  int buttonState5 = digitalRead(pinbutton1); // Joystick
  int buttonState6 = digitalRead(pinbutton6); // Read button 5 state
  int buttonState7 = digitalRead(pinbutton7); // Read button 5 state
  //square(&x,&y,5, 0);

  if (buttonState1 == 1) {
    while (digitalRead(pinbutton5)==1){}
    // Button 1 pressed, perform straight line

    //start
    digitalWrite(ledPin, HIGH);

    pen_control(UP,&penstate);
    x=0.0;
    y=0.0;
    delay(500);
    get_angles(x,y,L1,L2,&teta1, &teta2);
    servo1.write(teta1); 
    servo2.write(teta2);  
    delay(1000);

    pen_control(DOWN,&penstate);
    delay(500);

    //function
    straight_line(&x,&y,4, radians(90));

    //end
    pen_control(UP,&penstate);
    delay(500);
    digitalWrite(ledPin, LOW);
  } 

  if (buttonState2 == 1) {
    while (digitalRead(pinbutton2)==1){}
    // Button 1 pressed, perform straight line

    //start
    digitalWrite(ledPin, HIGH);

    pen_control(UP,&penstate);
    x=0.0;
    y=0.0;
    delay(500);
    get_angles(x,y,L1,L2,&teta1, &teta2);
    servo1.write(teta1); 
    servo2.write(teta2);  
    delay(1000);

    pen_control(DOWN,&penstate);
    delay(500);

    //function
    dotted_line(&x, &y, 4, radians(90), 0.5, 0.5);
    //straight_line(&x,&y,5, radians(90));

    //end
    pen_control(UP,&penstate);
    delay(500);
    digitalWrite(ledPin, LOW);
  } 

  //circle
  if (buttonState3 == 1) {
    while (digitalRead(pinbutton3)==1){}
    // Button 1 pressed, perform straight line

    //start
    digitalWrite(ledPin, HIGH);

    pen_control(UP,&penstate);
    x=1.0;
    y=1.0;

    //function
    circle(1, 1, 0, 360, 2.5, &x, &y, 0, 12);
    //straight_line(&x,&y,5, radians(90));

    //end
    pen_control(UP,&penstate);
    delay(500);
    digitalWrite(ledPin, LOW);
  } 

  //dotted circle
  if (buttonState4 == 1) {
    while (digitalRead(pinbutton4)==1){}
    // Button 1 pressed, perform straight line

    //start
    digitalWrite(ledPin, HIGH);

    pen_control(UP,&penstate);
    x=1.0;
    y=1.0;

    //function
    dotted_circle(1, 1, 10, 10, 2.5, &x, &y);

    //end
    pen_control(UP,&penstate);
    delay(500);
    digitalWrite(ledPin, LOW);
  } 

  //Joystick in processing
  if (buttonState6 == 1) {
    while (digitalRead(pinbutton6)==1){}
    digitalWrite(ledPin, HIGH);
    Joystick(&x,&y); 
    digitalWrite(ledPin, LOW);
  }

  if (buttonState7 == 1) {
    while (digitalRead(pinbutton7)==1){}
    // Button 1 pressed, perform straight line

    //start
    digitalWrite(ledPin, HIGH);

    pen_control(UP,&penstate);
    x=1.0;
    y=1.0;

    //function
    square(&x,&y,4, 0);
    //straight_line(&x,&y,5, radians(90));

    //end
    pen_control(UP,&penstate);
    delay(500);
    digitalWrite(ledPin, LOW);
  } 

  //Manual control of the robot using joystic
  if (buttonState5 == 0) {
    //Allows a smooth operation when a button is pushed (detect one time the tap)
    while (digitalRead(pinbutton1)==0){}

    digitalWrite(ledPin, HIGH);
    pen_control(UP,&penstate);
    x=0.0;
    y=0.0;
    delay(500);
    get_angles(x,y,L1,L2,&teta1, &teta2);
    servo1.write(teta1); 
    servo2.write(teta2);  
    delay(1000);

    pen_control(DOWN,&penstate);
    delay(500);

    double coef= 0.0003;
  
    while(digitalRead(pinbutton1)==1){
      //If the button is pressed then the effector is swithcing mode. For instance, if it was in writing position it goes UP and if it was UP then it gets into writing position.
      if (digitalRead(pinbutton5) == 1) {
        while (digitalRead(pinbutton5)==1){}
        pen_control(SWITCH,&penstate);
      }

      // Read analog values
      xtemp = int(512.0 - analogRead(pinx));
      ytemp = int(512.0 - analogRead(piny));

      // Apply dead zone for small movements
      if (abs(xtemp) <= 100) xtemp = 0;
      if (abs(ytemp) <= 100) ytemp = 0;

      // Update x and y coordinates
      x += xtemp * coef;
      y += ytemp * coef;

      Serial.print(x);
      Serial.print("\t");
      Serial.println(y);

      get_angles(x,y,L1,L2,&teta1, &teta2); //calculate motors' angles
      servo1.write(teta1);  //send data to the motors
      servo2.write(teta2);
      delay(10);

    }
    while (digitalRead(pinbutton1)==0){}
    digitalWrite(ledPin, LOW);
    pen_control(UP,&penstate);
    delay(500);
  }

}
```

### **Améliorations possibles**

Il existe quelques améliorations qu'on pourrait effecteur pour que le prototype du robot LineaScribe soit plus performant et efficace.

1. Ajouter des pieds anti-friction sur la base du robot.
2. Conceptualiser un plan de design avec possibilité d'être monté sur le châssis du robot.
3. Utilisez beaucoup moins de boutons pour basculer entre les différents modes de fonctionnement via la détection du nombre d'appuis sur un bouton par exemple.
4. Pour obtenir un cercle parfait, il faudrait modifier l’angle d’écriture du stylo sur la moitié du cercle. De cette façon, il n’y aura pas de dimensionnement. Ceci s'explique par le fait que les coordonnées calculées concernent le point de montage de notre effecteur (outil) et non jusqu'au point de contact avec la surface du papier.

### **Journal de bord / Calendrier**

*Avancée du projet à chaque étape, difficultés rencontrées, modifications et adaptations*

##### 14/02/2024

Discussion autour du Projet Robotique ROB3 - différents idées, décision, planning.

##### 16/02/2024

Création du schéma cinématique, de la table DH. Etablissement d'un premier modèle géométrique

##### 19/02/2024

Finalisation du dossier de conception préliminaire. Mise a jour du modèle géométrique et de la table DH, création du modèle géométrique inverse

##### 22/02/2024

Début de modélisation des pièces du robot

##### 24/02/2024

Recherche sur les méthodes de géométrie inverse du robot

##### 02/03/2024

Finalisation de la partie modèle géométrique directe et inverse

##### 08/03/2024

Impression des pièces du bâti support et on a lancé l'impression 3D du "pivot motor"

##### 24/04/2024

Programmation des fonctions lignes et carré (pour tests) et connexion au joystick.

##### 25/04/2024

Début de la fonction joystick. Assemblage et câblage définitif du robot. Programmation du cercle pour l'exercice 1

##### 22/05/2024

Finalisation du joystick. Programmation de la fonction pointillés

##### 23/05/2024

Finalisations du Joystick en mode Processing. Tests finaux et présentation

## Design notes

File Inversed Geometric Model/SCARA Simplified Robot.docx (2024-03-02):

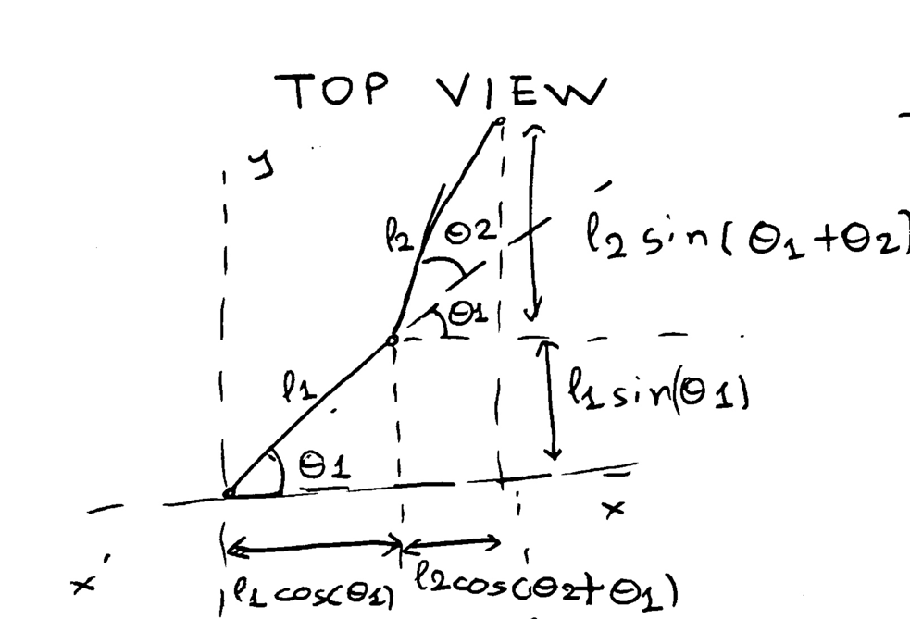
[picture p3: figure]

Direct Kinematics | Analysis

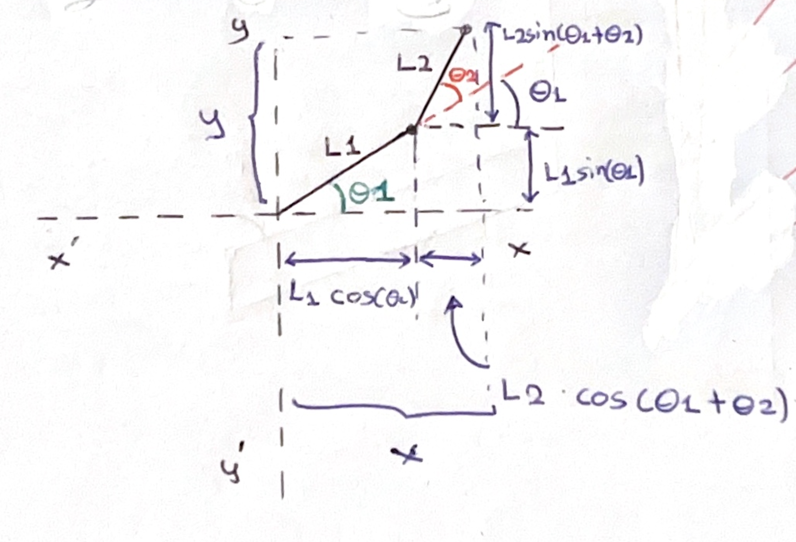
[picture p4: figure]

| We observe that: x = L1 cos(θ1) + L2 cos(θ1 + θ2) y = L1 sin(θ1) + L2 sin(θ1 + θ2) which is the direct kinematics analysis for the robot for its two first articulations We set φ = θ1 + θ2
Inversed Kinematics | Analysis

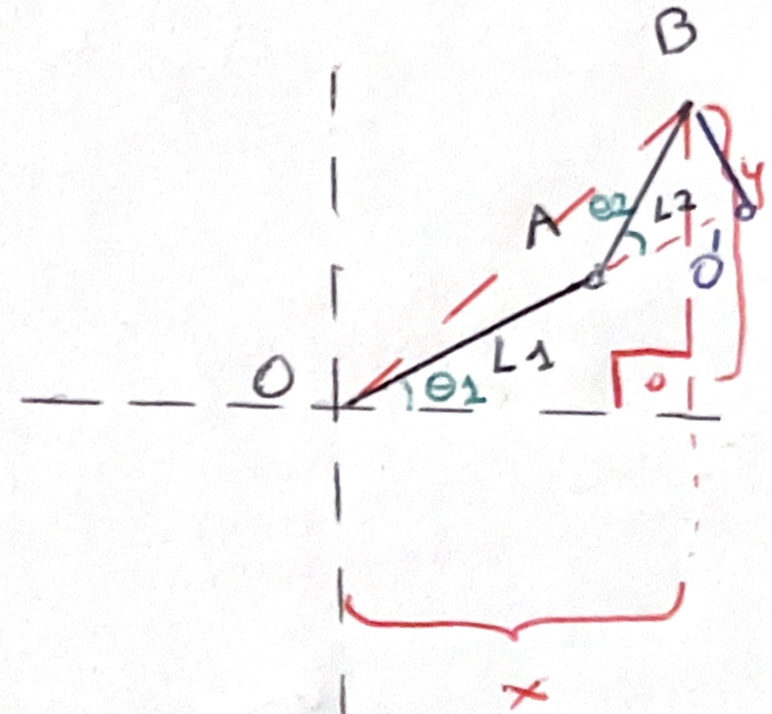
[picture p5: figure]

| From Pythagora’s theorem: OB^2 =x^2 + y^2 Moreover OB^2 = (L1 + L2 cos(θ2))^2 + (L2 sin(θ2))^2 = L2^2 sin(θ2)^2 + L1^2 + L2^2 cos(θ2)^2 +2 L1 L2 cos(θ2) ⟺ x^2 + y^2 - L1^2 - L2^2 (cos(θ2)^2 + sin(θ2)^2 ) = 2 L1 L2 cos(θ2)

So we take:

x^2 + y^2 - L1^2 - L2^2 = 2 L1 L2 cos(θ2) ⟺ cos(θ2) = (x^2 + y^2 - L1^2 - L2^2)/(2 L1 L2)

θ2 = arcos((x^2 + y^2 - L1^2 - L2^2)/(2 L1 L2))

Now for θ1:

φ = θ1 + θ2 ⟺ θ1 = φ - θ2 but what if we don’t know φ? Well, in that case:

ABO^(') triangle: sin(θ2) = √(1 - cos(θ2)^2)

ΒΟAcorner of BOO^(') triangle: ΒΟAcorner =arctan( (BO')/(L1 + AO'))= arctan( (L2sin(θ2))/(L1 + L2cos(θ2)))

Let’s say that ΒΟAcorner + θ1 = γ so:

θ1 = γ - ΒΟAcorner = arctan(y/x) - arctan( (L2sin(θ2))/(L1 + L2cos(θ2)))

Analyse simplifié – V1.8.3

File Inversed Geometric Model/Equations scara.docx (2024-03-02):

On a le Tableau DH suivant: , ai, αi, di+1, θi+10, 0, 0, h1, θ11, L1, -π/2, h2, θ2-π/22, 0, 0, L2, θ3

T_(0→1) = (cos⁡(θ1), -sin⁡(θ1), 0, 0sin⁡(θ1), cos⁡(θ1), 0, 00, 0, 1, h10, 0, 0, 1)=A

Pour un robot du type SCARA, sur la matrice de transformation homogene suivante, il faut avoir au lieu de’avoir θ2 – θ1 – π/2, θ2. Ici on a remplacé θ2 par θ2 – θ1 – π/2 car pour le même tableau DH on a fait une preuve (disponible sur Wiki) permettant de sans changer de tableau DH, de trouver l’équation pour notre robot parallélépipède.

T_(1→2) = (cos⁡(θ2-π/2), -sin⁡(θ2-π/2), 0, L10, 0, 1, h2-sin⁡(θ2-π/2), -cos⁡(θ2-π/2), 0, 00, 0, 0, 1)

T_(2→effector) = (cos⁡(θ3), -sin⁡(θ3), 0, 0sin⁡(θ3), cos⁡(θ3), 0, 00, 0, 1, L20, 0, 0, 1)

Ainsi pour T_(0→2) on a:

T_(0→2) = (cos[θ1]sin[θ2], cos[θ1]cos[θ2], -sin[θ1], L1cos[θ1]-h2sin[θ1]sin[θ2]sin[θ1], sin[θ1]cos[θ2], cos[θ1], h2cos[θ1]+L1sin[θ1]cos[θ2], -sin[θ2], 0, h10, 0, 0, 1)

parce que (cos(θ1), -sin(θ1), 0, 0sin(θ1), cos(θ1), 0, 00, 0, 1, h10, 0, 0, 1) . (cos(θ2-π/2), -sin(θ2-π/2), 0, L10, 0, 1, h2-sin(θ2-π/2), -cos(θ2-π/2), 0, 00, 0, 0, 1)= (cos⁡(θ1), -sin⁡(θ1), 0, 0sin⁡(θ1), cos⁡(θ1), 0, 00, 0, 1, h10, 0, 0, 1) . (cos⁡(θ2-π/2), sin⁡(-θ2+π/2), 0, L10, 0, 1, h2sin⁡(-θ2+π/2), -cos⁡(θ2-π/2), 0, 00, 0, 0, 1)= (cos⁡(θ1), -sin⁡(θ1), 0, 0sin⁡(θ1), cos⁡(θ1), 0, 00, 0, 1, h10, 0, 0, 1) . (cos⁡(-θ2+π/2), sin⁡(-θ2+π/2), 0, L10, 0, 1, h2sin⁡(-θ2+π/2), -cos⁡(-θ2+π/2), 0, 00, 0, 0, 1) = (cos⁡(θ1), -sin⁡(θ1), 0, 0sin⁡(θ1), cos⁡(θ1), 0, 00, 0, 1, h10, 0, 0, 1) . (sin(θ2), cos(θ2), 0, L10, 0, 1, h2cos(θ2), -sin(θ2), 0, 00, 0, 0, 1)= (cos[θ1]sin[θ2], cos[θ1]cos[θ2], -sin[θ1], L1cos[θ1]-h2sin[θ1]sin[θ2]sin[θ1], sin[θ1]cos[θ2], cos[θ1], h2cos[θ1]+L1sin[θ1]cos[θ2], -sin[θ2], 0, h10, 0, 0, 1)

car cos(-x) = cos(x)

car sin(-x) = -sin(x)

Maintenant on multiplie T_(0→2) . T_(2→effector) pour obtenir T_(0→effector) . Alors:

T_(0→effector) = (cos[θ1]Cos[θ3]sin[θ2]+cos[θ1]cos[θ2]Sin[θ3], cos[θ1]cos[θ2]Cos[θ3]-cos[θ1]sin[θ2]Sin[θ3], -sin[θ1], L1cos[θ1]-h2sin[θ1]-L2sin[θ1]Cos[θ3]sin[θ1]sin[θ2]+cos[θ2]sin[θ1]Sin[θ3], cos[θ2]Cos[θ3]sin[θ1]-sin[θ1]sin[θ2]Sin[θ3], cos[θ1], h2cos[θ1]+L2cos[θ1]+L1sin[θ1]cos[θ2]Cos[θ3]-sin[θ2]Sin[θ3], -Cos[θ3]sin[θ2]-cos[θ2]Sin[θ3], 0, h10, 0, 0, 1)= (cos[θ1](Cos[θ3]sin[θ2]+cos[θ2]Sin[θ3]), cos[θ1](cos[θ2]Cos[θ3]-sin[θ2]Sin[θ3]), -sin[θ1], L1cos[θ1]-(h2+L2)sin[θ1]sin[θ1](Cos[θ3]sin[θ2]+cos[θ2]Sin[θ3]), sin[θ1](cos[θ2]Cos[θ3]-sin[θ2]Sin[θ3]), cos[θ1], (h2+L2)cos[θ1]+L1sin[θ1]cos[θ2]Cos[θ3]-sin[θ2]Sin[θ3], -Cos[θ3]sin[θ2]-cos[θ2]Sin[θ3], 0, h10, 0, 0, 1)

Maintenant les coordonnées de notre stylo dans R3 sont P3=(p1001) . Ses coordonnées dans R0 seront donc :

(, L1cos[θ1]-(h2+L2)sin[θ1]+p1cos[θ1](Cos[θ3]sin[θ2]+cos[θ2]Sin[θ3]), (h2+L2)cos[θ1]+L1sin[θ1]+p1sin[θ1](Cos[θ3]sin[θ2]+cos[θ2]Sin[θ3]), h1+p1(cos[θ2]Cos[θ3]-sin[θ2]Sin[θ3]), 1)=P0

qu’on obtenu en faisant: P0= T_(0→effector) . P3

P0’s homogenous notation is: (, L1cos[θ1]-(h2+L2)sin[θ1]+p1cos[θ1](Cos[θ3]sin[θ2]+cos[θ2]Sin[θ3]), (h2+L2)cos[θ1]+L1sin[θ1]+p1sin[θ1](Cos[θ3]sin[θ2]+cos[θ2]Sin[θ3]), h1+p1(cos[θ2]Cos[θ3]-sin[θ2]Sin[θ3]))= (, -((h2+L2)sin[θ1])+cos[θ1](L1+p1Cos[θ3]sin[θ2]+p1cos[θ2]Sin[θ3]), (h2+L2)cos[θ1]+sin[θ1](L1+p1Cos[θ3]sin[θ2]+p1cos[θ2]Sin[θ3]), h1+p1cos[θ2]Cos[θ3]-p1sin[θ2]Sin[θ3])

Now we are solving the linear system (, x, y, z)= (, -((h2+L2)sin[θ1])+cos[θ1](L1+p1Cos[θ3]sin[θ2]+p1cos[θ2]Sin[θ3]), (h2+L2)cos[θ1]+sin[θ1](L1+p1Cos[θ3]sin[θ2]+p1cos[θ2]Sin[θ3]), h1+p1cos[θ2]Cos[θ3]-p1sin[θ2]Sin[θ3]) to find θ1, θ2, θ3

Calcul des matrices pour notre robot - V2.1.2

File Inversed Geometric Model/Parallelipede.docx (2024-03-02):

We know that L1=L2 and L3=L4 , as well as L1 || L2 and L3 || L4 . θ1 and θ2 can rotate around O (0,0) independently while respecting the following condition 0 ≤ θ1 + θ2 ≤ 180 . We are searching to express xd and yd in relation with L1, L2, θ1, θ2, etc.

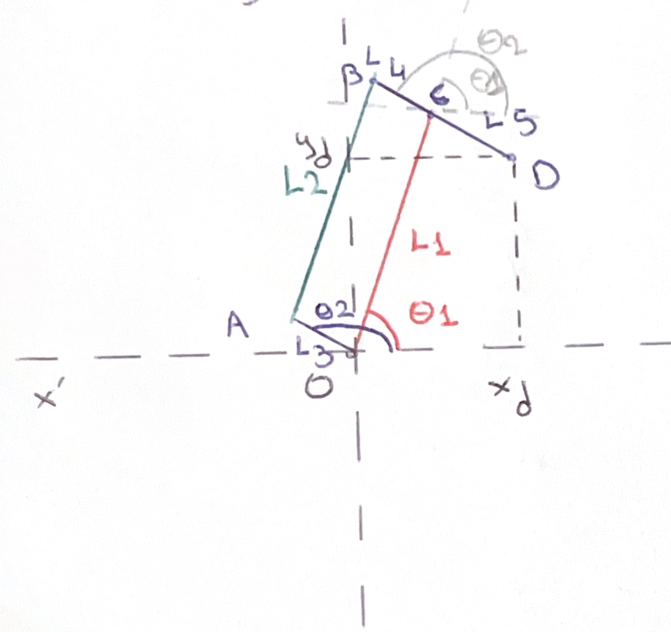
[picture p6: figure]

Step | Analysis

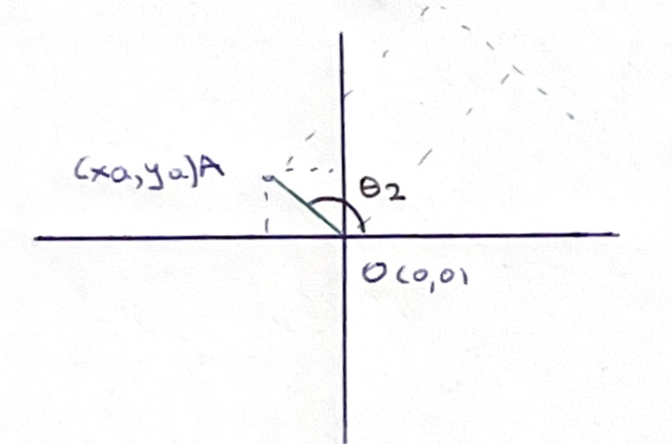
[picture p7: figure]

| θ2=arctan((ya)/(xa)) car tan(θ)= y/x

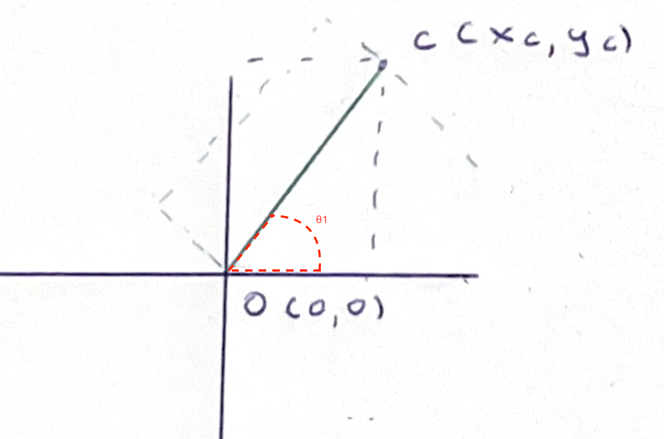
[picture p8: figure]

| θ1=arctan⁡((yc)/(xc))

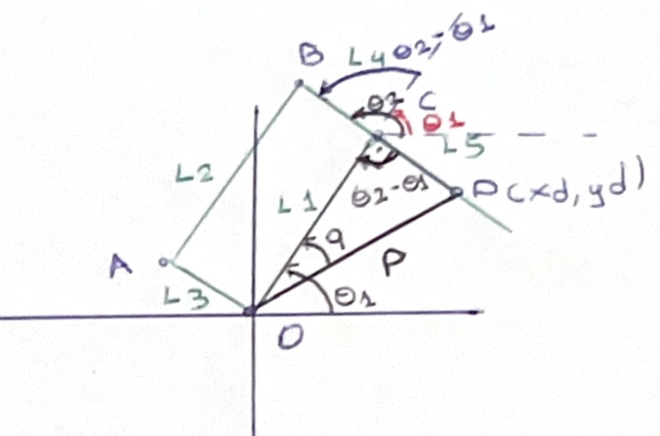
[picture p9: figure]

| From cosinus lema we have: p^2 =L1^2 +L5^2 -2 L1 L2cos(θ2-θ1) so p=√(L1^2 +L5^2 -2 L1 L2cos(θ2-θ1)) and from sinus lema we have: (sin⁡(q))/(L5)=(sin⁡(θ2-θ1))/p ⟺sin(q)=(L5)/psin⁡(θ2-θ1)

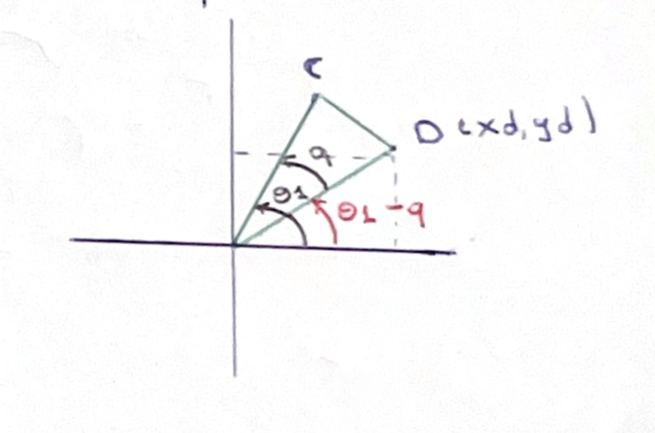
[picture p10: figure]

| xd=p cos(θ1-q) yd=p sin(θ1-q)

so by replacing q and p from previous step we take:

xd = √(L1^2 +L5^2 -2 L1 L2cos(θ2-θ1)) cos (θ1 - arcsin((L5)/(√(L1^2 +L5^2 -2 L1 L2cos(θ2-θ1)))sin⁡(θ2-θ1))

and

yd = √(L1^2 +L5^2 -2 L1 L2cos(θ2-θ1)) sin (θ1 - arcsin((L5)/(√(L1^2 +L5^2 -2 L1 L2cos(θ2-θ1)))sin⁡(θ2-θ1))

Analyse parallélépipède – V1.0.1

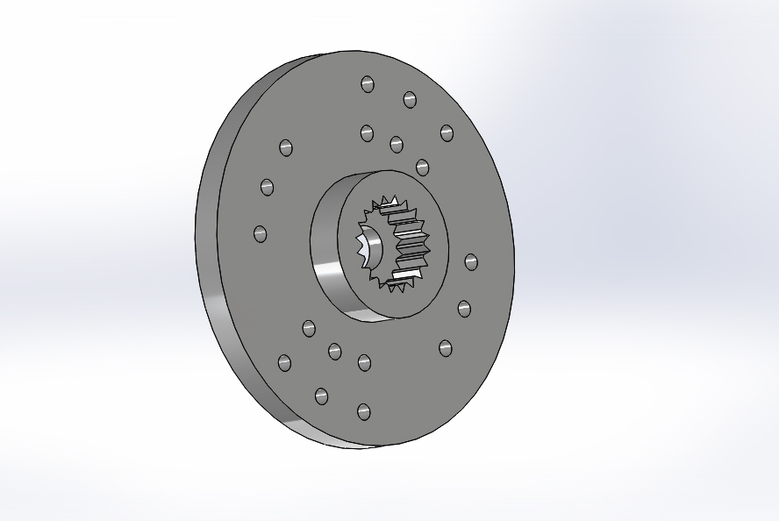
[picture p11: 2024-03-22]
CAO/Ressources/hitec-hs-422-servo-horn-disc-1.snapshot.1/hs-422_disc_sws(2).JPG

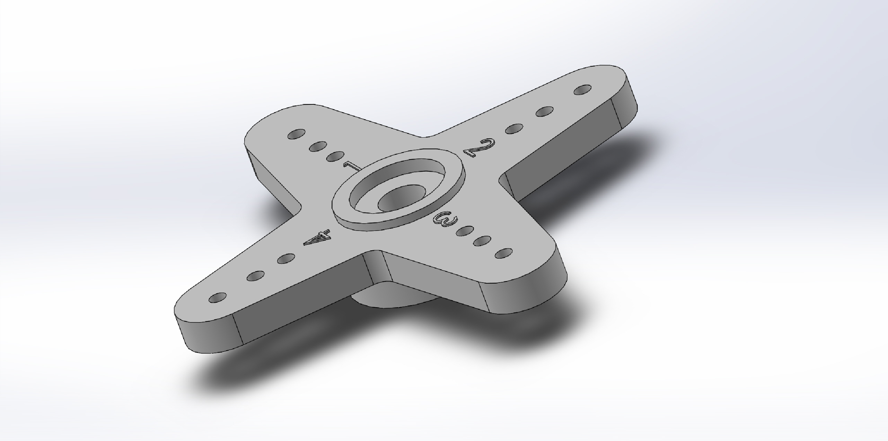
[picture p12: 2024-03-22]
CAO/Ressources/hitec-hs-422-servo-horn-4-wings-1.snapshot.2/hs-422_horn_4wings_sws(1).JPG

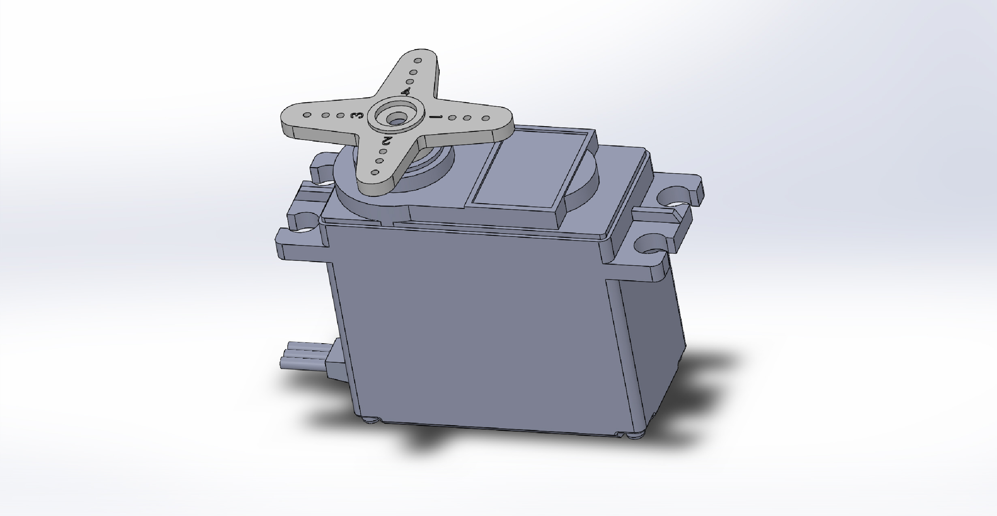
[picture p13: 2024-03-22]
CAO/Ressources/hitec-hs-422-servo-horn-4-wings-1.snapshot.2/hs-422_horn_4wings_sws(2).JPG

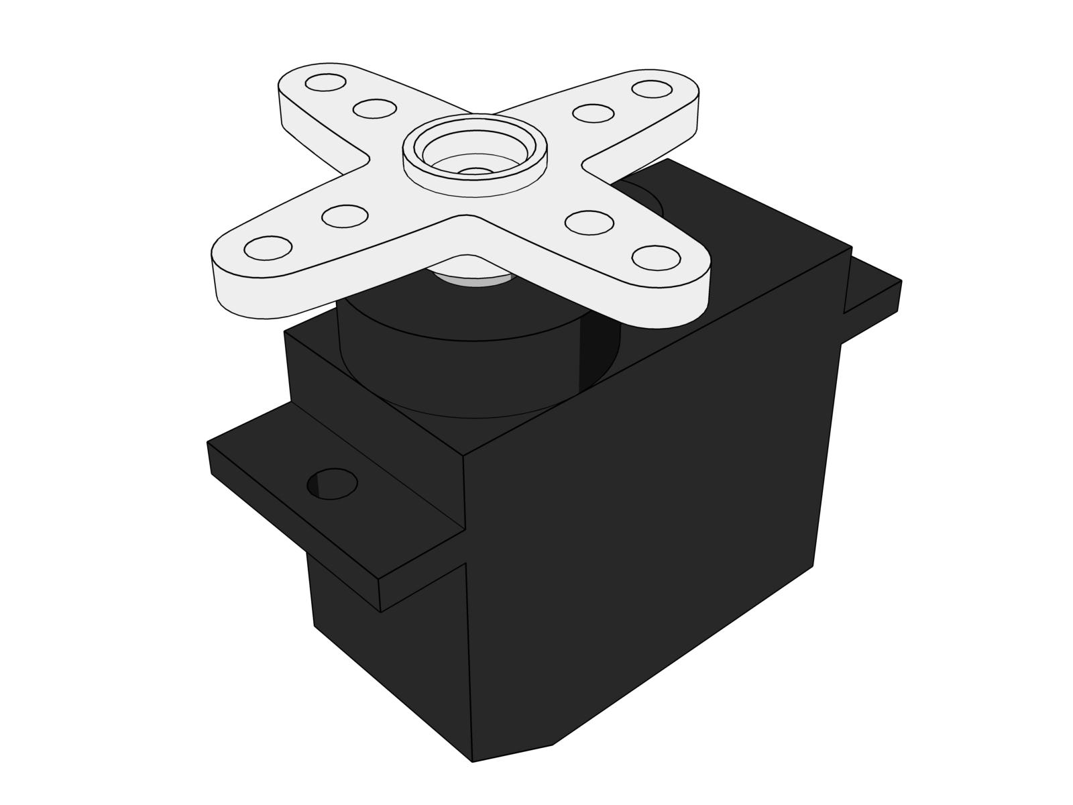
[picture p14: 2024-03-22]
CAO/Ressources/emax-es08aii-1.snapshot.1/EMAX es08A servo 01.jpg

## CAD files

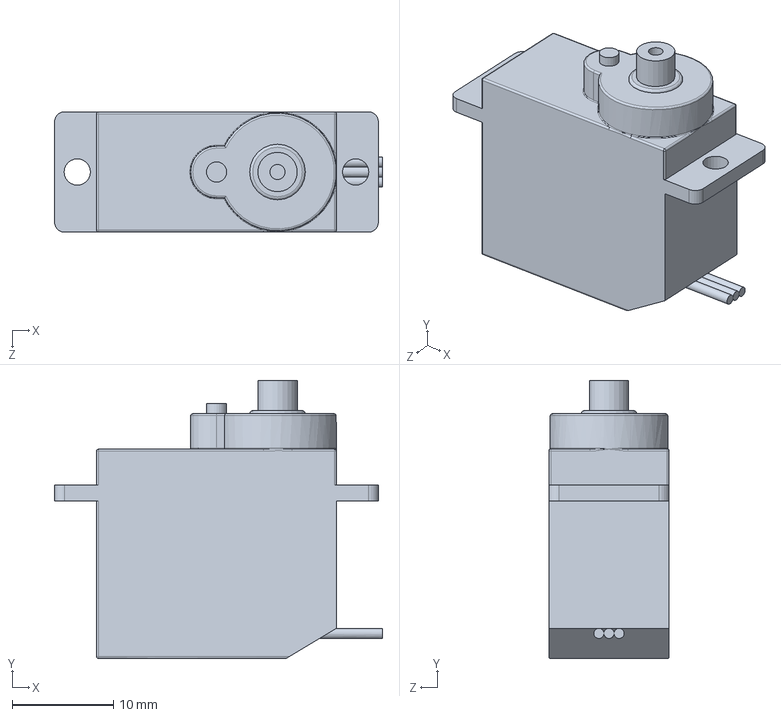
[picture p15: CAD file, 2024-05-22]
CAO/Ressources/emax-es08aii-1.snapshot.1/EMAX_ES08AII_Micro_Servo.SLDPRT
32.4 x 27.5 x 11.9 mm

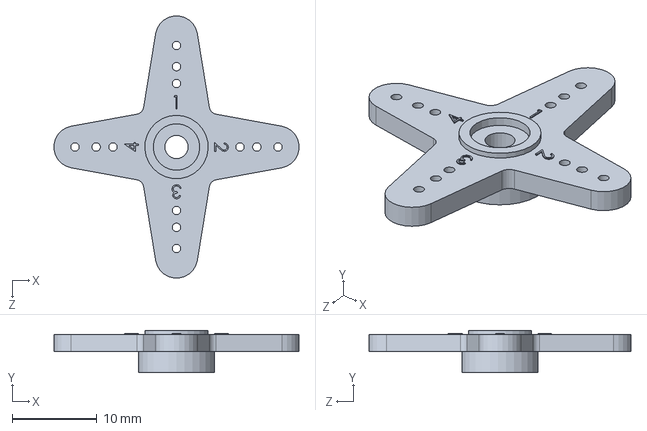
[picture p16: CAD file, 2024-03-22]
CAO/Ressources/hitec-hs-422-servo-horn-4-wings-1.snapshot.2/hs-422_horn_4wings_sws.SLDPRT
29.0 x 5.00 x 31.0 mm

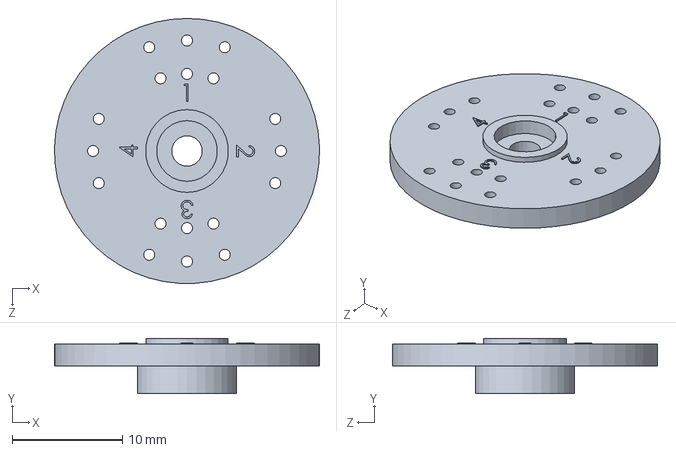
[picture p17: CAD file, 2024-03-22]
CAO/Ressources/hitec-hs-422-servo-horn-disc-1.snapshot.1/hs-422_horn_disc_sws(1).SLDPRT
24.0 x 5.00 x 24.0 mm

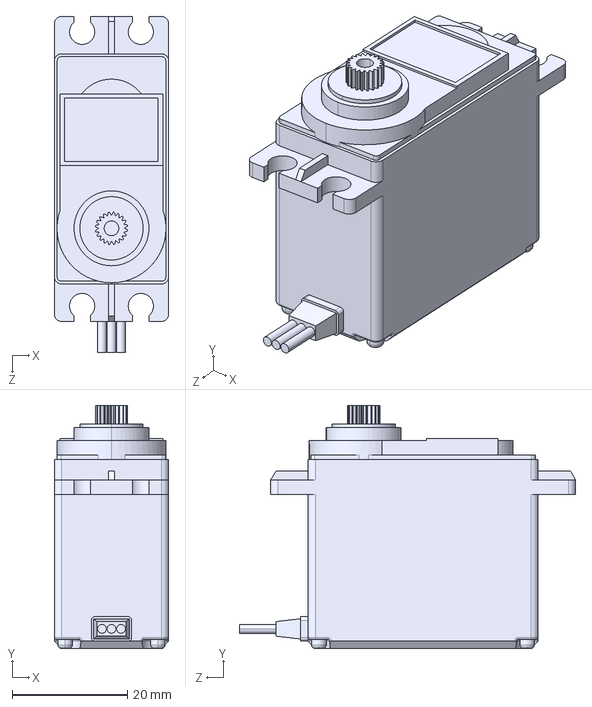
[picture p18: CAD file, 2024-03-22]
CAO/Ressources/hitec-hs-422-standard-servo-motor-1.snapshot.3/hs-422_sws.STEP
19.8 x 42.1 x 58.2 mm

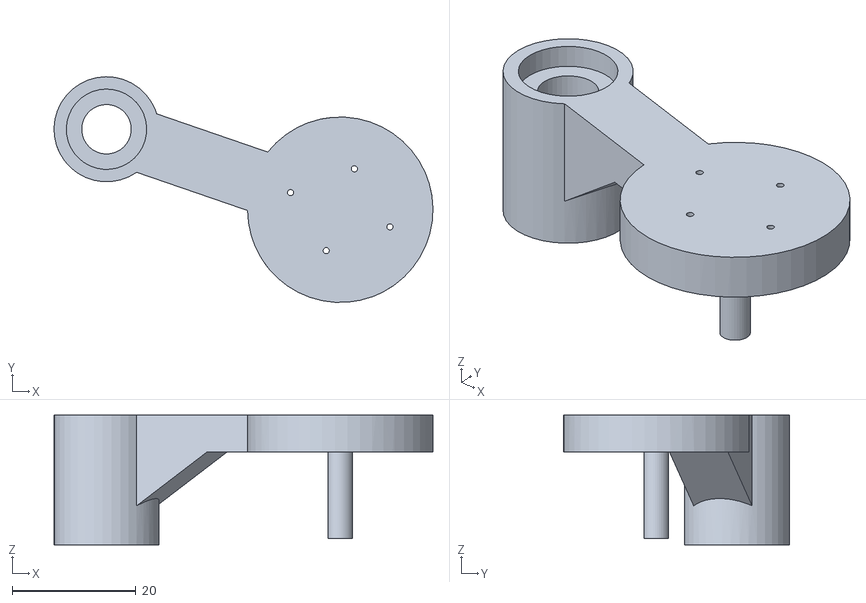
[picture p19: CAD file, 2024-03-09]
Conception (SVGs, STLs)/pivot motor.STL
61.3 x 36.5 x 21.0

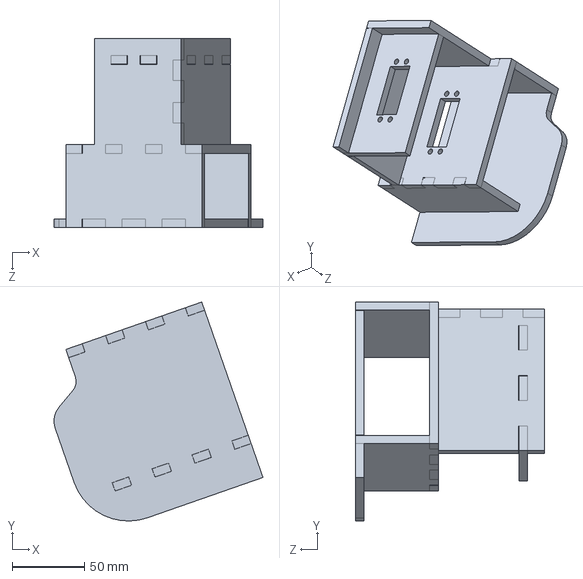
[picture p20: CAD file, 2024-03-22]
CAO/Assemblage Tour/Tour.SLDPRT
145.1 x 152.1 x 131.5 mm

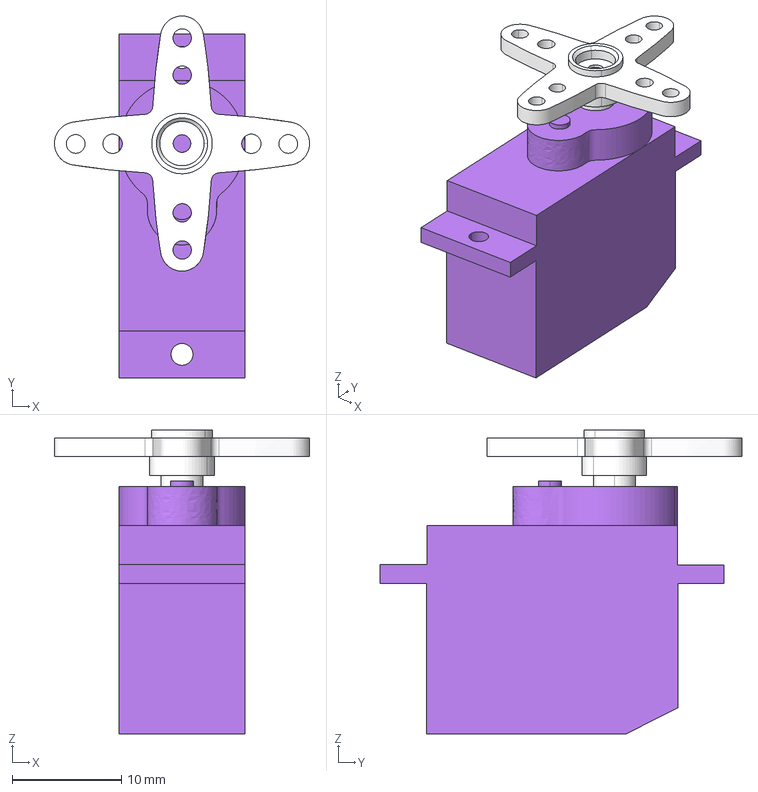
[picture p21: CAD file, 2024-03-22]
CAO/Ressources/emax-es08aii-1.snapshot.1/EMAX es08A servo.stp
23.3 x 33.1 x 27.8 mm

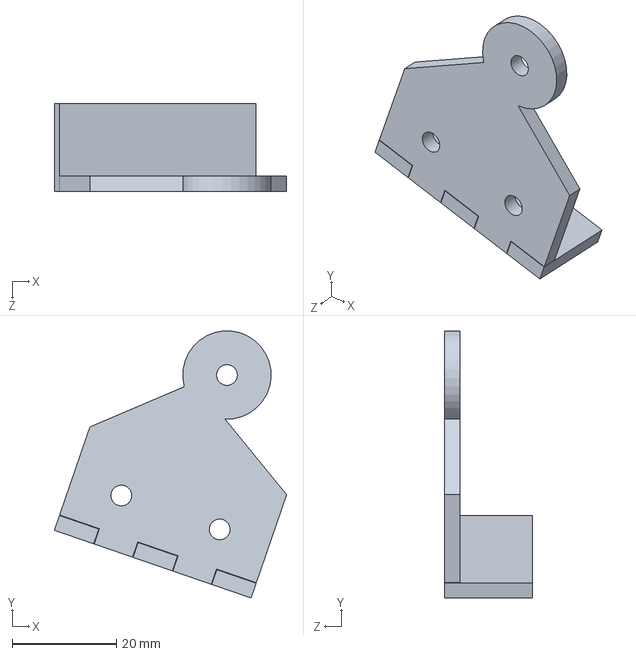
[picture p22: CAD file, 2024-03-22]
CAO/Assemblage Bras/Pièce Liaison Billette Principale -Billette Emax.SLDPRT
44.7 x 51.3 x 17.0 mm

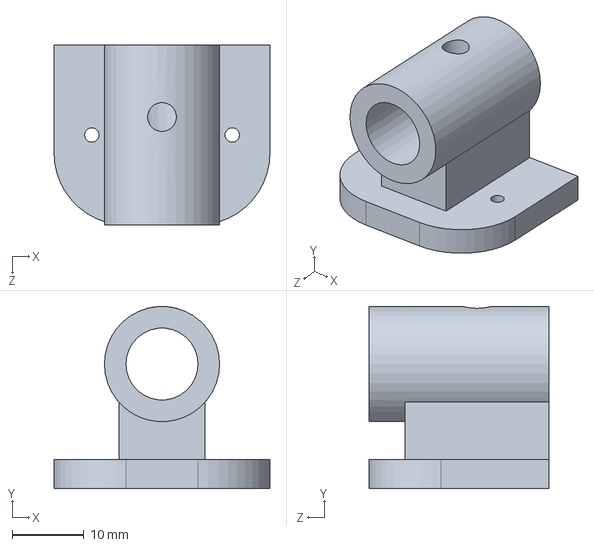
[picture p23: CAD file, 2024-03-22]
CAO/Assemblage Bras/Effecteur.SLDPRT
30.0 x 25.3 x 25.0 mm

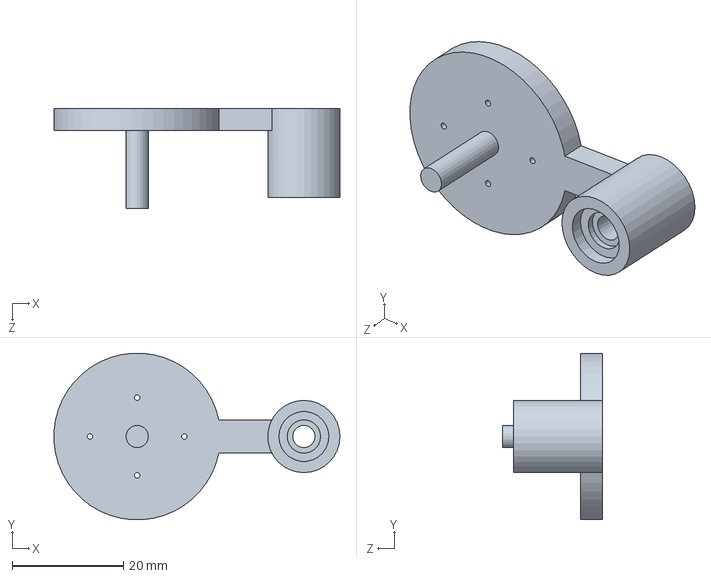
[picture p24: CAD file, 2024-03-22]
CAO/Assemblage Bras/ActionneurServo.SLDPRT
51.5 x 29.9 x 18.0 mm

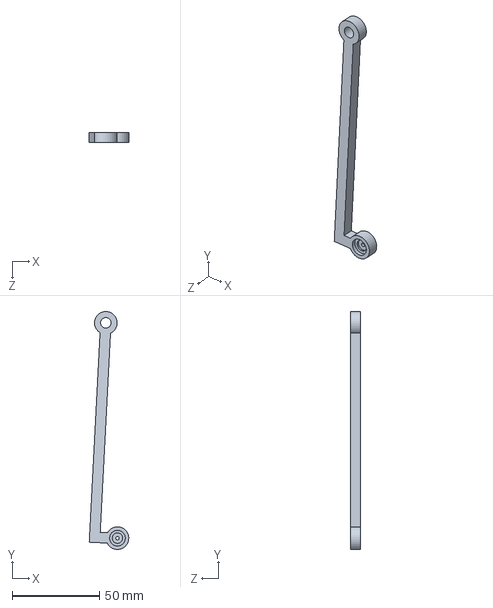
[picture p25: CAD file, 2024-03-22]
CAO/Assemblage Bras/Billette Emax.SLDPRT
22.6 x 136.1 x 6.00 mm

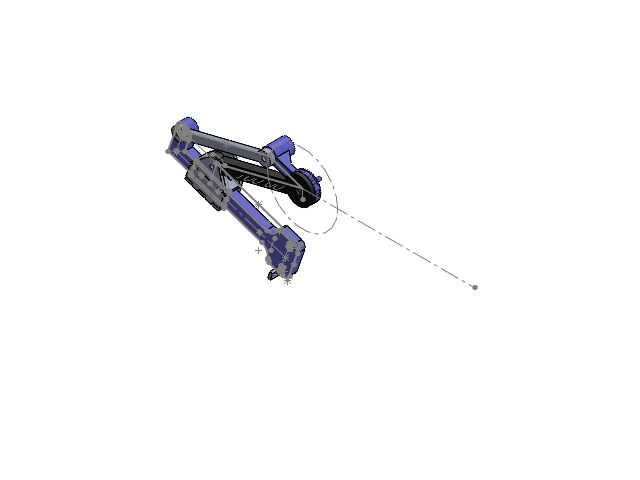
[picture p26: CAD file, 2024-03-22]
CAO/Architecture.SLDASM
Billette Principale
Billette Secondaire
Billette Emax
Pièce Liaison Billette Principale -Billette Emax
ActionneurServo
Pignon Servo Emax

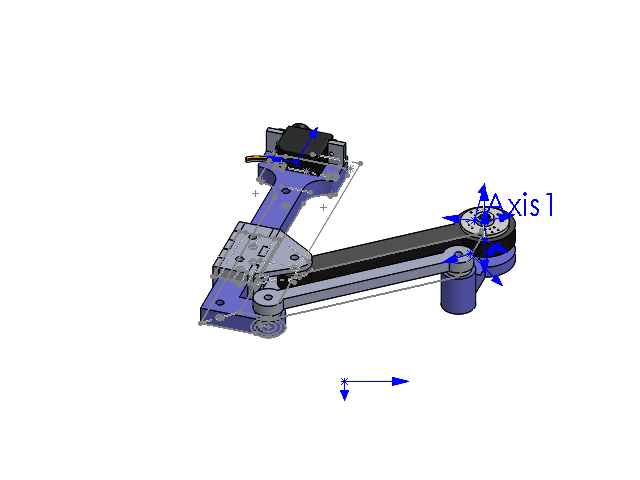
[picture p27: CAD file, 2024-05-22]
CAO/Assemblage Bras/Liaison axe.SLDASM
angular contact ball bearing_68_iso x 6
Billette Principale
Billette Emax
Billette Secondaire
hs-422_horn_disc_sws(1) x 2
plain washer normal grade a_iso x 5
ActionneurServo
Pièce Liaison Billette Principale -Billette Emax
Pignon Servo Emax x 2
EMAX_ES08AII_Micro_Servo

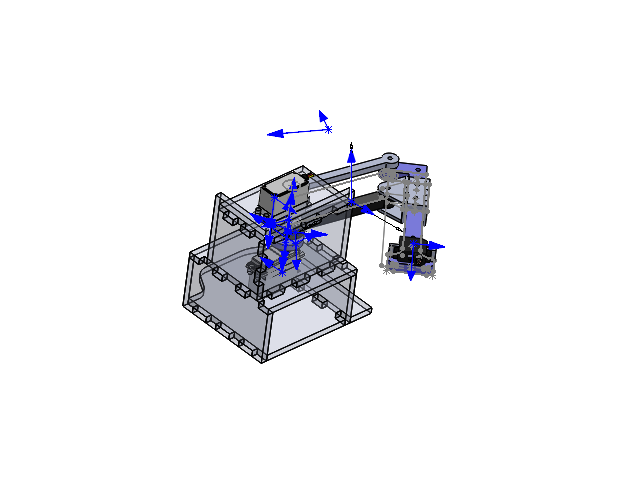
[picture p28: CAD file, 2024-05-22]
CAO/Assemblage Tour/Assemblage1.SLDASM
angular contact ball bearing_68_iso x 6
Billette Principale
Billette Emax
Billette Secondaire
hs-422_horn_disc_sws(1) x 2
plain washer normal grade a_iso x 5
ActionneurServo
Pièce Liaison Billette Principale -Billette Emax
Pignon Servo Emax x 2
EMAX_ES08AII_Micro_Servo
hs-422_sws x 2
Tour

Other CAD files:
CAO/Assemblage Bras/Pignon Servo Emax.SLDPRT
CAO/Assemblage Bras/Billette Principale.SLDPRT
CAO/Assemblage Bras/Billette Secondaire.SLDPRT
CAO/Ressources/emax-es08aii-1.snapshot.1/Emax ES08AII.ipt
CAO/Ressources/hitec-hs-422-standard-servo-motor-1.snapshot.3/hs-422_sws.SLDPRT

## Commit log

2024-03-22 updated 22/03/24
    [ActionneurServo.SLDPRT, Architecture.SLDASM, Assemblage1.SLDASM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]
2024-05-22 Final version (program not included)
    Corrections on CAO, as well as on equations systems.
    [Assemblage1.SLDASM, EMAX_ES08AII_Micro_Servo.SLDPRT, Liaison axe.SLDASM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]
2024-05-22 Files re-roganisation
    [ActionneurServo.SLDPRT, Architecture.SLDASM, Assemblage1.SLDASM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]
